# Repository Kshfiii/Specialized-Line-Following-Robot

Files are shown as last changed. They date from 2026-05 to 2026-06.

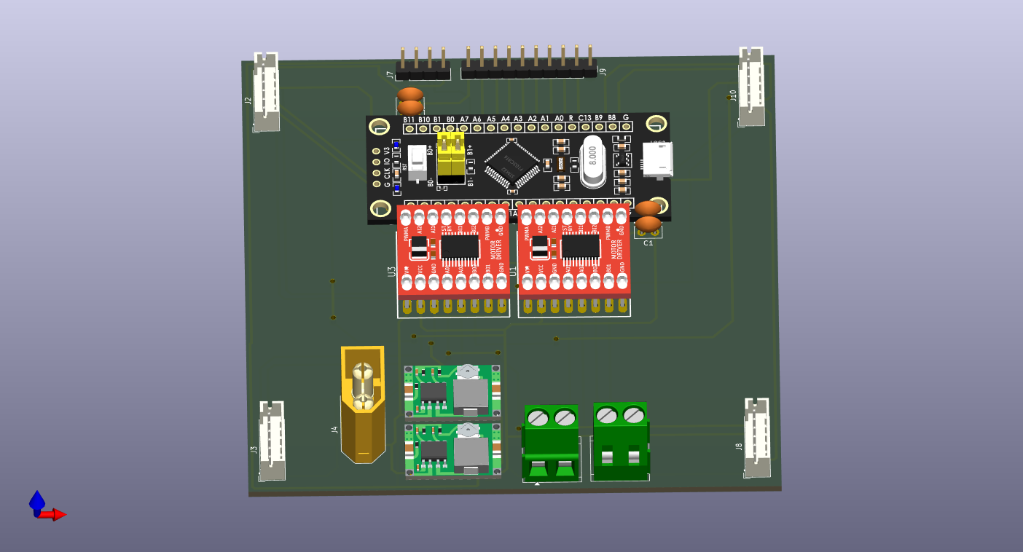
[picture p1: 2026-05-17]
PCB/LFR_Specialized.png

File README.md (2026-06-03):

# Specialized-Line-Following-Robot
Github (1000 x 350 px)

This is a specialized line follower robot with a custom built 8 Sensor Array, using tcrt5000 IR sensors, for sensing the lines. In addition to basic line following, the robot has a specialized function for dispensing pellets into designated spots, at different heights, for which it uses a scissor lift along with a conveyor belt system, powered by high torque n20 motors. It was made to compete in a robotics competition, NERC, and as a way to challenge myself to make a better LFR then the one I made before, which I think I have.

## About

<!-- This Project is powered by an 11.1v 3300 mah Li-po battery. It has 3 power rails; 11.1v, 5v, and <!- 3rd power line here ->, it uses two mini mp2307 to convert the voltages.-->
### 1. Robot function 
 
 
 

The robot follows a 3cm wide black line on the arena floor, maneuvering intersections & Zig Zag patterns on the arena floor. At Storage rack 1 (S1), a box of 7x7 inches supports the storage rack, with one of four faces colored blue. the robot must go around the box to detect the blue colored face, where the slot openings are present in the form of a 2x2 grid, as seen in the image above. The robot must detect strips below the slots as either blue or red, placing the pellets into the slots marked blue, and skipping over the red ones. The robot then heads to Storage rack 2 (S2), repeating the same procedure. Then, the robot travels through the zig zag pattern and climbs a ramp to reach Storage rack 3 (S3), After sucessful dispensing into designated slots at S3, it parks itself beyond the red line. 

### 2. Body
The body consists of three layers. The Base, the Middle, and the top most layer. 
 #### 2.1 The Base
Roboto (3)
The base is made of a custom 3d printed Chasis, housing four GA25-370 Motors and a battery on top with the IR Sensor Array Mounted to the bottom, Alongside extruded platforms for inserts.

##### 2.1.1 IR Sensor Array
Roboto (3)

<!-- add ss of 3d model from kicad & schematics-->
A custom built 8 channel analog IR sensor array bulit from tcrt5000 sensors. It uses 4.7k & 1k resistors. It also utilizes capacitors & an led that lights up when a sensor is returning a reading, serving as a checker to see if it works. 

#### 2.2 The Middle layer
Roboto (1)

<!-- add ss of middle layer from onshape, make a banner thing with lables in canva and put it here, layer has, acrylic base, spacers, pcb, hcsr04  -->
The Middle layer is supported by a laser cut acrylic sheet which is screwed on top of the 3d printed chasis using spacers. It consists of a custom built PCB & spacers along with the HC-SR04 ultrasonic sensor for distance measurement. 

##### 2.2.1 PCB
Roboto (5)
The pcb routes a 3300mah, 11.1v li-po battery pack through two mini MP2307 buck convertor, forming 3 power rails, 11.1v, 5v, and <!-- x volts --> which are used throughout the robot. The PCB houses the STM32F401 Microcontroller with two TB6612FNG motor driver breakout boards, one of which governs the motion of the GA25-370 motors and the other controls the N20 motors used for raising the scissor lift and moving the conveyor belt. It has headers for the IR sensors and the ultrasonic sensor.

#### 2.3 The Top layer
Roboto (8)
The top layer is also supported by a laser cut acrylic sheet which is screwed on top of the first acrylic sheet, separated by ~1.2in vertically, using spacers and nuts. It is home to the whole Pellet dispensing mechanism, The scissor lift, the Color sensing system and the conveyor belt.

##### 2.3.1 Scissor lift
<!-- add ss of 3d model from onshape, make a banner thing with lables in canva and put it here -->
The scissor lift is made entriely of a 3d printed body. It's movement is controlled by a high torque N20 gear motor which sits on the acrylic sheet. The collapsed height of the lift is <!-- x inches --> and it can streatch upto <!-- y inches --> 

##### 2.3.2 Color sensing system
<!-- add ss of 3d model from onshape, make a banner thing with lables in canva and put it here -->
The color sensing system consists of a Sg90 servo with a TCS34725 color sensor mounted to a 3d printed arm, which is screwed onto Sg90. The arm is <!-- z inches --> in length. The system is fixed underneath the top plate of the scissor lift, so that it can climb with the lift, giving it the ability to detect the color of the strips at both heights vertically. The servo rotates the arm 180° which allows the color sensor to detect both heights laterally. By using this system, the color sensor can cover the strips below each slot in the 2x2 grid.

##### 2.3.3 Conveyor belt
<!-- add ss of 3d model from onshape with the pellets stored and dimensions, make a banner thing with lables in canva and put it here -->
The conveyor belt is made of a 3d printed body. It uses a high torque N20 motor and bearings to rotate the pulleys, which drive the belt. The pellets sit on top of the belt, preloaded before the robot starts. 

## Assembly & Building
Go to [Onshape](https://cad.onshape.com/documents/1d0c454716dc1fb7909d87f9/w/77de741c5d18967e566ddcde/e/cc4241ede1b87dd95ef516c6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) Each part of the Line follower robot has been organized into folders. All print parts are consolidated in the 'To Print' tab on the bottom left. If confusion persists, you may contact me at: kasshafemman@gmail.com. Now follow along for each section.

### Body
Open the LFR Body Folder to see the CAD model. Now, using the brackets, fix the motors to the chasis. Put the wheels on the motor shaft. Put the insrts into the extruded square, then use it to screw Acrylic layer one. Put the PCB on this layer and the Ultrasonic sensor, within its bracket. Add a spacer and screw in Acrylic layer 2. Then put the scissor lift's extruded patterns (for the lack of a better word) on top of the complimentary slots on Acrylic layer 2.

### Scissor Lift:
Open Scissor lift folder for reference. Slide the scissor legs onto the shafts and put them in the place holders made on platform one. Use a string or pice of yarn, tying one end to the n20 motor and the other to the center of shaft 2. To prevent the shafts from sliding off, attach the knubs to the shaft's complementery ends. Now put pin 1 through one end of the hole in the scissor leg and pin 2 through the other, repeat this for all the arms to get the scissors pattern as shown in the assembly.

### Conveyor Belt
Open conveyor belt folder for reference. Put the supports into side plate 1 of the conveyor belt. Glue in bearings in the holes of both plates and put the pulleys inside the bearings. Now attach Side plate 2 on the other side. Put the conveyor belt onto the scissor lift, which had complementary holes to have it fixed in place.

## Robot Logic & Software
It is written in C++ using the Arduino framework on an STM32F401 (Black Pill). The code is split into six files, 'drive', 'sensors', 'Lift', 'nav' (short for navigation', 'pellet dispension' (color sensing + conveyor belt), with each of them handling one specific robot fuction, plus an additional 'config.h' where I put the tunable values.

Navigation is handled by the nav.cpp file, which uses a PID logic and values from the IR sensor array to stay on the line. The Wheel encodersb give additional feedback, measuring the distance traveled, and the HC-SR04 ultrasonic sensor confirms when the robot is close enough to a rack for dispensing.

At each station, the robot scans the rack using the color sensing mechanism. The TCS34725 is aligned so that it faces the colored strip. It takes several readings at its position, so that it can detect the color of the strip reliably. If the strip is blue, the robot alligns itself with the rack and a pellet is dispensed. After that, the servo rotates 180°, sensing the other strip laterally. The process is repeated for both the lower and upper rows of the rack, the lift raises the sensor and dispenser to reach the upper row. Additionally, Color readings are normalized to reduce the effect of changing lighting conditions.

The robot follows the black line, navigating to S1, dropping the pellets, Then repeating the same for S2, then climbs the ramp to S3, drops the pellets and parks itself beyond the finsih line. `nav.cpp` handles line following using a PID controller on the IR array's weighted error, with encoder ticks tracking distance from the last known point and the HC-SR04 confirming when the rack face is actually in range.

The servicing routine is the same for all three units. The robot closes in on the rack, sweeps the color sensor servo left and right at the lower row, reads the TCS34725 five times per position, nudges left or right and ejects into whichever slots came back blue, then raises the lift and repeats for the upper row. Color detection normalizes against the clear channel so arena lighting doesn't throw it off.

### Dependencies
To work, the firmware needs:
- STM32duino core
- `Adafruit_TCS34725` via Arduino Library Manager
- `Wire` and `Servo` ship with the core

## Component List
1. STM32F401 (Blackpill) Microcontroller
2. B6612FNG Motor Driver
3. JGA25-370 Motor with wheels and Brackets
4. TCRT5000 IR sensors
5. Resistors and capacitors
6. 11.1v 3300mAh Lipo Battery
7. High torque N20 Motors
8. TCS34725 Color Sensor
9. Hc-sr04 Ultrasonic Sensor
10. Bearings
11. Acrylic sheet

## Bill of Materials
| Component | Quantity | Est. Cost (USD) | Purchase Links | 
| :--- | :---: | :--- | :--- |
| **PLA Filament**| 1 | $16.55 |[Link](https://electrobes.com/product/exyz-pla-1-75mm-3d-printer-filament-1kg-roll/)| 
| **11.1v 3300mAh Lipo Battery** | 1 | $24.00 | [Link](https://colgroad.com/product/zop-power-3s-11-1v-3300mah-25c-lipo-battery/) | 
| **JGA25-370 Motor kit** | 4 | $48.00 | [Link](https://colgroad.com/product/dc-gear-motor-with-encoder-280rpm-620rpm-ga25-370-complete-kit/)| 
| **TCRT5000 IR sensors** | 10 | $03.40 |[Link](https://epro.pk/product/tcrt5000-reflective-optical-ir-sensor-in-pakistan/)| 
| **Resistors** | 2 | $00.50 |[Link](https://epro.pk/product/1206-smd-resistor-smd-1206-tolerance-5-smd-resistor-1206-pack-of-10-pcs-2/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)| 
| **SMD LED** | 2 | $00.75 |[Link](https://digilog.pk/products/100pcs-smd-0805-led-smt-led-light-diode?variant=49762233876758)| 
| **Hc-sr04 Ultrasonic Sensor** | 1 | $00.72 | [Link](https://epro.pk/product/ultrasonic-sensor-hc-sr04-in-pakistan/) | 
| **Standoff** | 2 | $00.25 |[Link](https://epro.pk/product/brass-standoff-spacer-screw-long-pillars-nut/)| 
| **Mp2307 Buck convertor** | 2 | $00.90 |[Link](https://epro.pk/product/dc-to-dc-step-down-mini-360-buck-converter-module/)| 
| **6 pin Jst-xh connector** | 4 | $00.14 |[Link](https://digilog.pk/products/6-pin-2-5mm-jst-xh-style-male-connector-in-pakistan)| 
| **Xt60 Lipo battery connector** | 1 | $00.65 |[Link](https://epro.pk/product/xt60connectorsmalefemalepairinpakistan/)| 
| **Sg90 Servo Motor** | 1 | $1.15 |[Link](https://epro.pk/product/tower-pro-sg90-9g-micro-servo-motor-with-accessories-blue/)| 
| **STM32F401**| 1 | $03.55 |[Link](https://epro.pk/product/stm32f401-development-board/)| 
| **TB6612FNG Motor Driver**| 1 | $02.00 | [Link](https://epro.pk/product/tb6612-drv8833-dual-motor-driver-module-1a-h-bridge-for-arduino-robotics/) | 
| **200 RPM N20 Motors** | 2 | $03.00 | [Link](https://colgroad.com/product/n20-mini-dc-gear-motor-200-600-800-1000-rpm-brand-new/) | 
| **TCS34725 Color Sensor** | 1 | $03.58 | [Link](https://digilog.pk/products/tcs34725-color-sensor-module-pakistan) | 
| **Bearings** | 1 | $4.30 | [Link](https://epro.pk/product/cnc-v-slot-bearing-open-builds-wheel-pom-mr105zz-625zz-bore-5mm-passive-round-gear/) | 
| **Acrylic sheet** | 2 | $03.23 | [Link](https://www.daraz.pk/products/acrylic-sheet-2mm-size-12x12-2mm-thick-i391245284.html)| 
| **Total Build Cost:** |  | **~$120.00** |

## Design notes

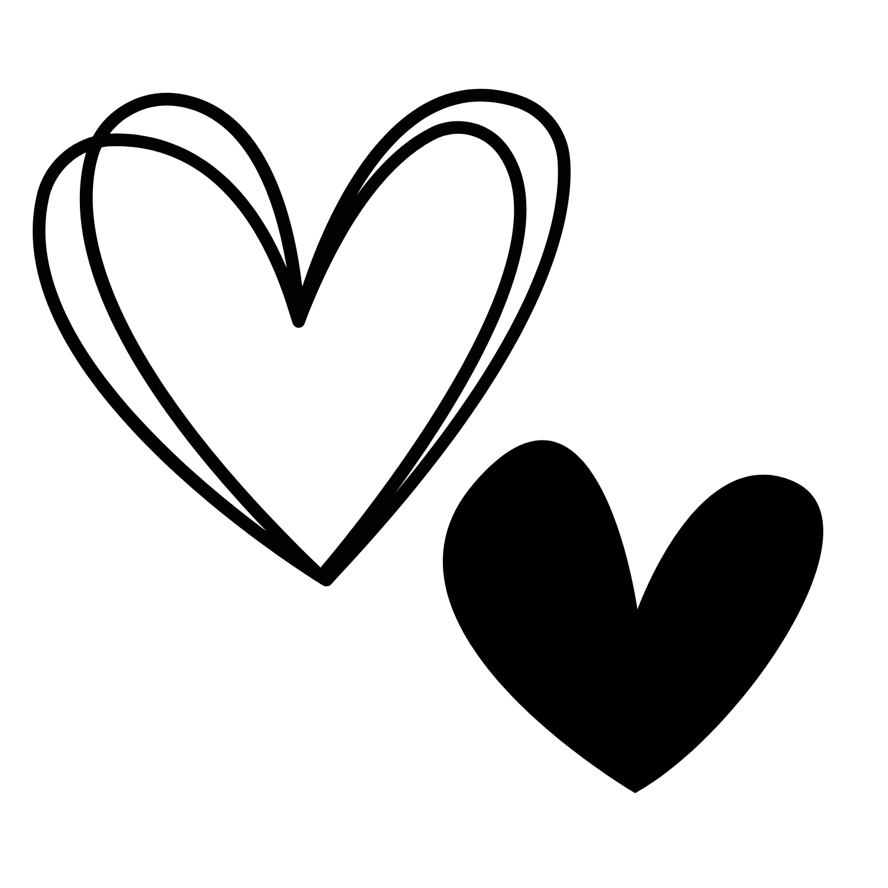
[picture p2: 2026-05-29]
IR_Array/Untitled design (2).png

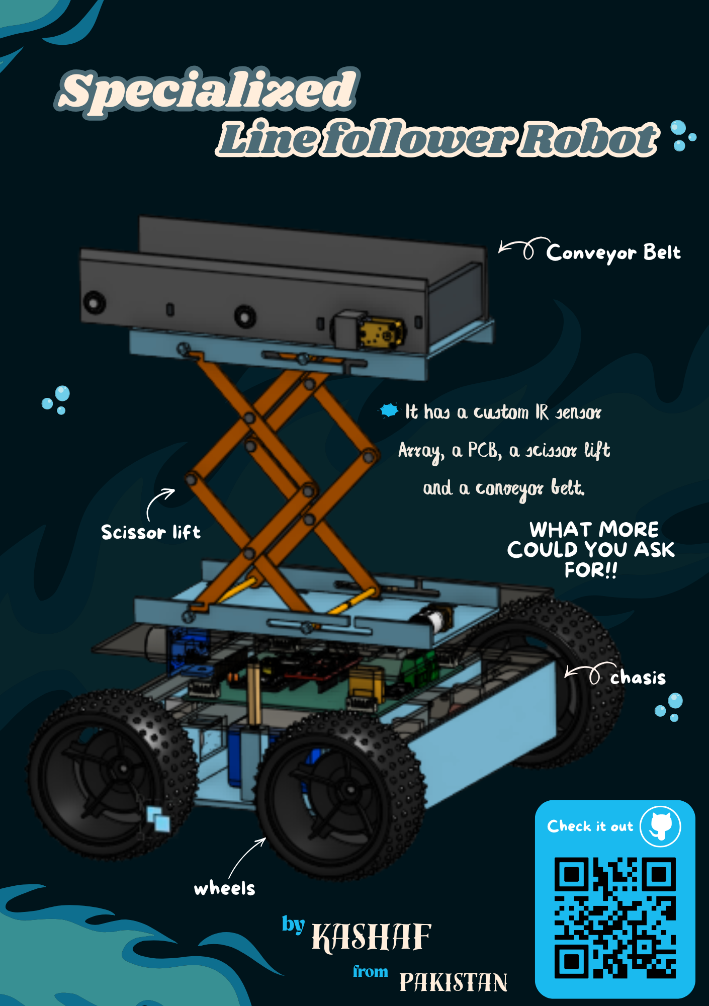
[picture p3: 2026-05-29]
LFR_Zine.png

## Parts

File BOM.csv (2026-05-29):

Component | Quantity | Est. Cost (USD) | Purchase Links
STM32F401 | 1 | $03.55 | https://epro.pk/product/stm32f401-development-board/
TB6612FNG Motor Driver | 1 | $02.00 | https://epro.pk/product/tb6612-drv8833-dual-motor-driver-module-1a-h-bridge-for-arduino-robotics/
JGA25-370 Motor kit | 4 | $24.00 | https://colgroad.com/product/dc-gear-motor-with-encoder-280rpm-620rpm-ga25-370/
QTR 8C IR Sensor Array | 2 | $04.59 | https://epro.pk/product/qtr-8rc-line-following-reflectance-ir-sensor-8-channel-line-following-line-tracking-array-module/
11.1v 3300mAh Lipo Battery | 1 | $24.00 | https://colgroad.com/product/zop-power-3s-11-1v-3300mah-25c-lipo-battery/
200 RPM N20 Motors | 2 | $03.00 | https://colgroad.com/product/n20-mini-dc-gear-motor-200-600-800-1000-rpm-brand-new/
TCS34725 Color Sensor | 1 | $03.58 | https://digilog.pk/products/tcs34725-color-sensor-module-pakistan
Hc-sr04 Ultrasonic Sensor | 1 | $00.72 | https://epro.pk/product/ultrasonic-sensor-hc-sr04-in-pakistan/
Bearings | 1 | $4.30 | https://epro.pk/product/cnc-v-slot-bearing-open-builds-wheel-pom-mr105zz-625zz-bore-5mm-passive-round-gear
Acrylic sheet | 2 | $03.23 | https://www.daraz.pk/products/acrylic-sheet-2mm-size-12x12-2mm-thick-i391245284.html
Total Build Cost: |  | ~$70.00

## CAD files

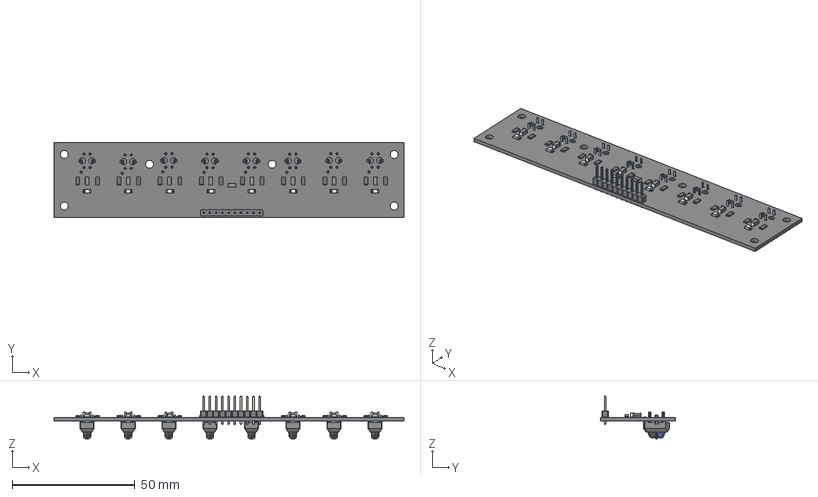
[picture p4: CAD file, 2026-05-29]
IR_Array/IR_Array.step
142.8 x 30.4 x 17.4 mm
C_1206_3216Metric x 9
R_1206_3216Metric x 16
LED_1206_3216Metric x 8
PinHeader_1x10_P2.54mm_Vertical
TCRT5000--3DModel-STEP-56544 x 8
IR_Array_PCB

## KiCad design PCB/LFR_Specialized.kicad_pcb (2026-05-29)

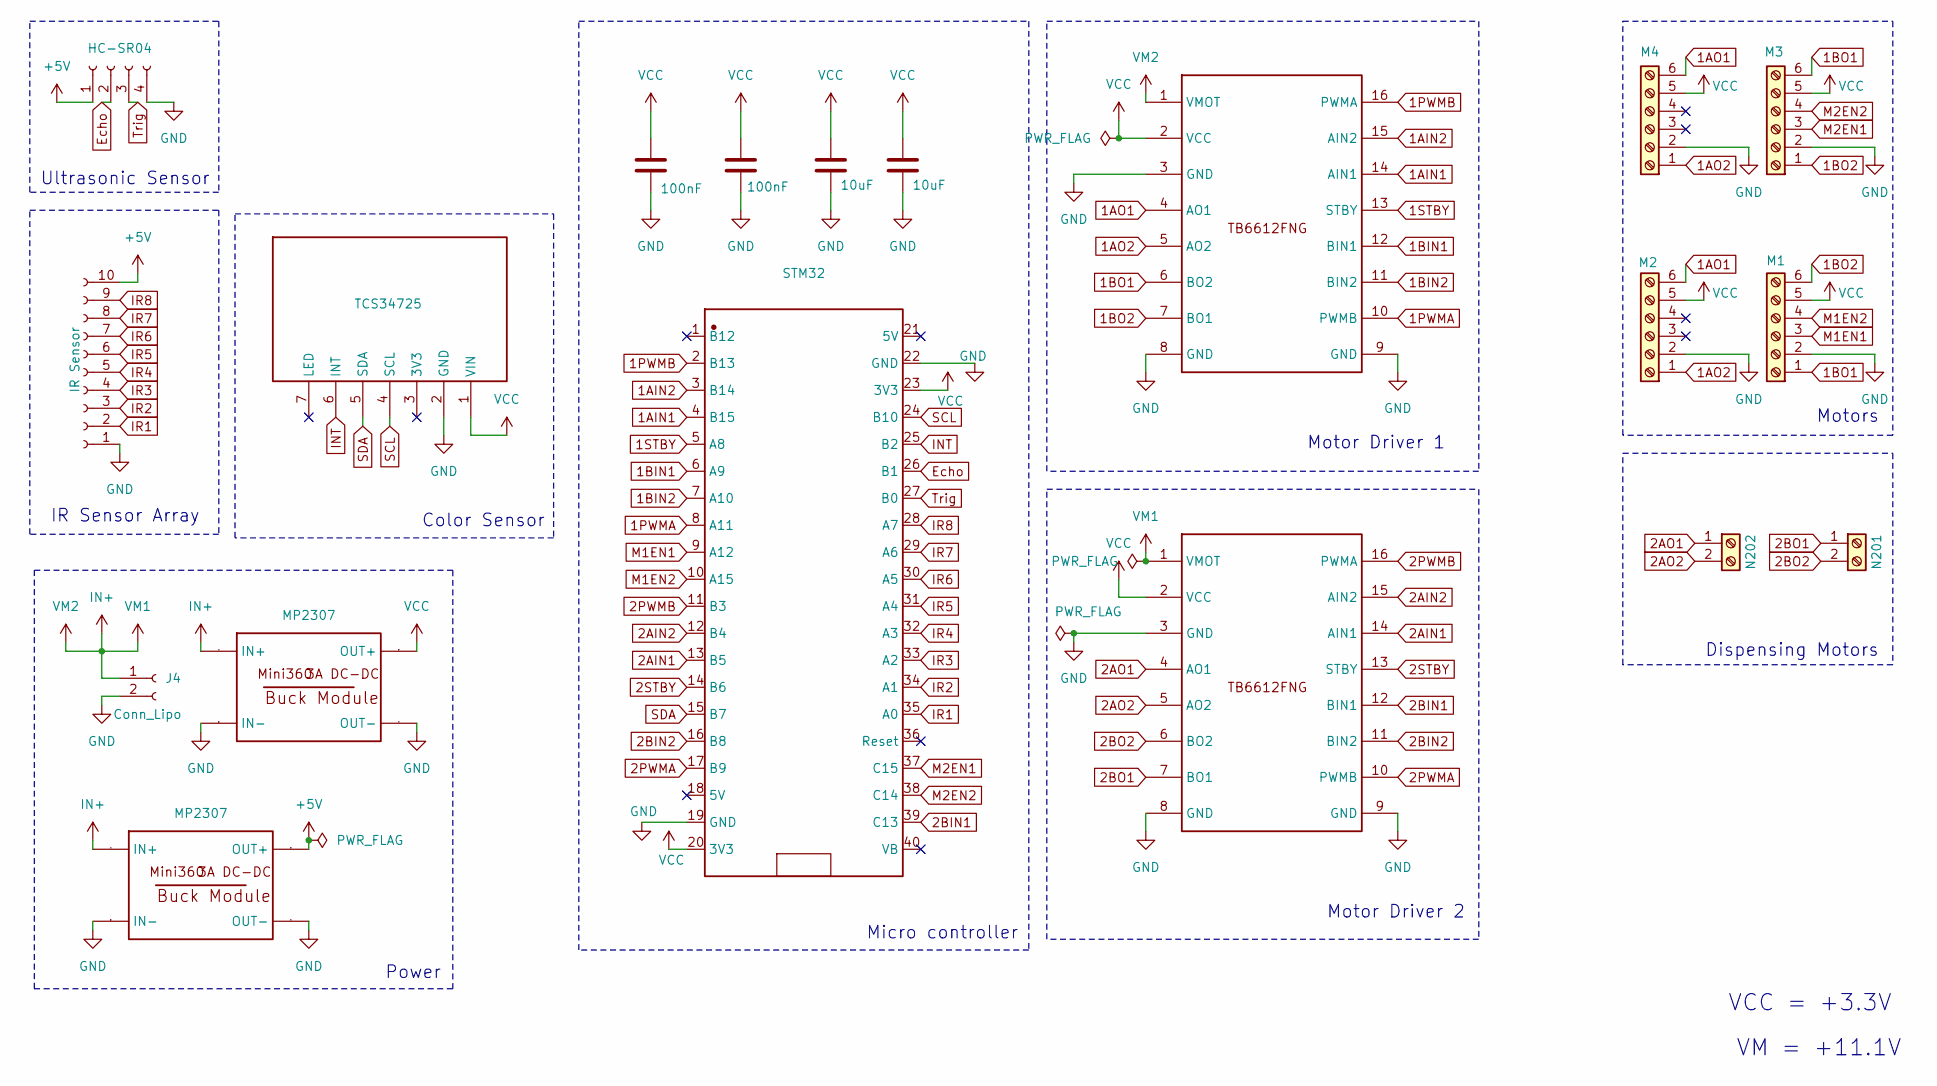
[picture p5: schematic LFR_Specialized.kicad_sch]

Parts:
C1, C12: 10uF; C_Disc_D5.0mm_W2.5mm_P2.50mm
C9, C11: 100nF; C_Disc_D5.0mm_W2.5mm_P2.50mm
J2: M1; JST_PH_B6B-PH-K_1x06_P2.00mm_Vertical
J3: M2; JST_PH_B6B-PH-K_1x06_P2.00mm_Vertical
J4: Conn_Lipo; AMASS_XT60-M_1x02_P7.20mm_Vertical
J5: N201; terminal
J6: N202; terminal
J7: HC-SR04; PinHeader_1x04_P2.54mm_Vertical
J8: M4; JST_PH_B6B-PH-K_1x06_P2.00mm_Vertical
J9: IR Sensor; PinHeader_1x10_P2.54mm_Vertical
J10: M3; JST_PH_B6B-PH-K_1x06_P2.00mm_Vertical
P1: TCS34725; PinHeader_1x07_P2.54mm_Vertical
STM32: STM32F401CC-WEACTBOARD-FOOTPRINT
U1, U3: TB6612FNG Dual Motor Driver SparkFun; TB6612FNG-BREAKOUT
U2, U4: MP2307; MINI360 BUCK CONVERTOR

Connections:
1AIN1: STM32.4 (B15), U3.14 (AIN1)
1AIN2: STM32.3 (B14), U3.15 (AIN2)
1AO1: J3.6, J8.6, U3.4 (AO1)
1AO2: J3.1, J8.1, U3.5 (AO2)
1BIN1: STM32.6 (A9), U3.12 (BIN1)
1BIN2: STM32.7 (A10), U3.11 (BIN2)
1BO1: J2.1, J10.6, U3.6 (BO2)
1BO2: J2.6, J10.1, U3.7 (BO1)
1PWMA: STM32.8 (A11), U3.10 (PWMB)
1PWMB: STM32.2 (B13), U3.16 (PWMA)
1STBY: STM32.5 (A8), U3.13 (STBY)
2AIN1: STM32.13 (B5), U1.14 (AIN1)
2AIN2: STM32.12 (B4), U1.15 (AIN2)
2AO1: J6.1, U1.4 (AO1)
2AO2: J6.2, U1.5 (AO2)
2BIN1: STM32.39 (C13), U1.12 (BIN1)
2BIN2: STM32.16 (B8), U1.11 (BIN2)
2BO1: J5.1, U1.7 (BO1)
2BO2: J5.2, U1.6 (BO2)
2PWMA: STM32.17 (B9), U1.10 (PWMB)
2PWMB: STM32.11 (B3), U1.16 (PWMA)
2STBY: STM32.14 (B6), U1.13 (STBY)
Echo: J7.2, STM32.26 (B1)
GND: C1.2, C9.2, C11.2, C12.2, J2.2, J3.2, J4.2, J7.4, J8.2, J9.1, J10.2, P1.2 (GND), STM32.19 (GND), STM32.22 (GND), U1.3 (GND), U1.8 (GND), U1.9 (GND), U2.1 (IN-), U2.3 (OUT-), U3.3 (GND), U3.8 (GND), U3.9 (GND), U4.1 (IN-), U4.3 (OUT-)
IN+: J4.1, U1.1 (VMOT), U2.2 (IN+), U3.1 (VMOT), U4.2 (IN+)
INT: P1.6 (INT), STM32.25 (B2)
IR1: J9.2, STM32.35 (A0)
IR2: J9.3, STM32.34 (A1)
IR3: J9.4, STM32.33 (A2)
IR4: J9.5, STM32.32 (A3)
IR5: J9.6, STM32.31 (A4)
IR6: J9.7, STM32.30 (A5)
IR7: J9.8, STM32.29 (A6)
IR8: J9.9, STM32.28 (A7)
M1EN1: J2.3, STM32.9 (A12)
M1EN2: J2.4, STM32.10 (A15)
M2EN1: J10.3, STM32.37 (C15)
M2EN2: J10.4, STM32.38 (C14)
SCL: P1.4 (SCL), STM32.24 (B10)
SDA: P1.5 (SDA), STM32.15 (B7)
Trig: J7.3, STM32.27 (B0)

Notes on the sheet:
VM = +11.1V
Ultrasonic Sensor
Power
Dispensing Motors
Motors
Micro controller
Motor Driver 2
Color Sensor
IR Sensor Array
Motor Driver 1
VCC = +3.3V

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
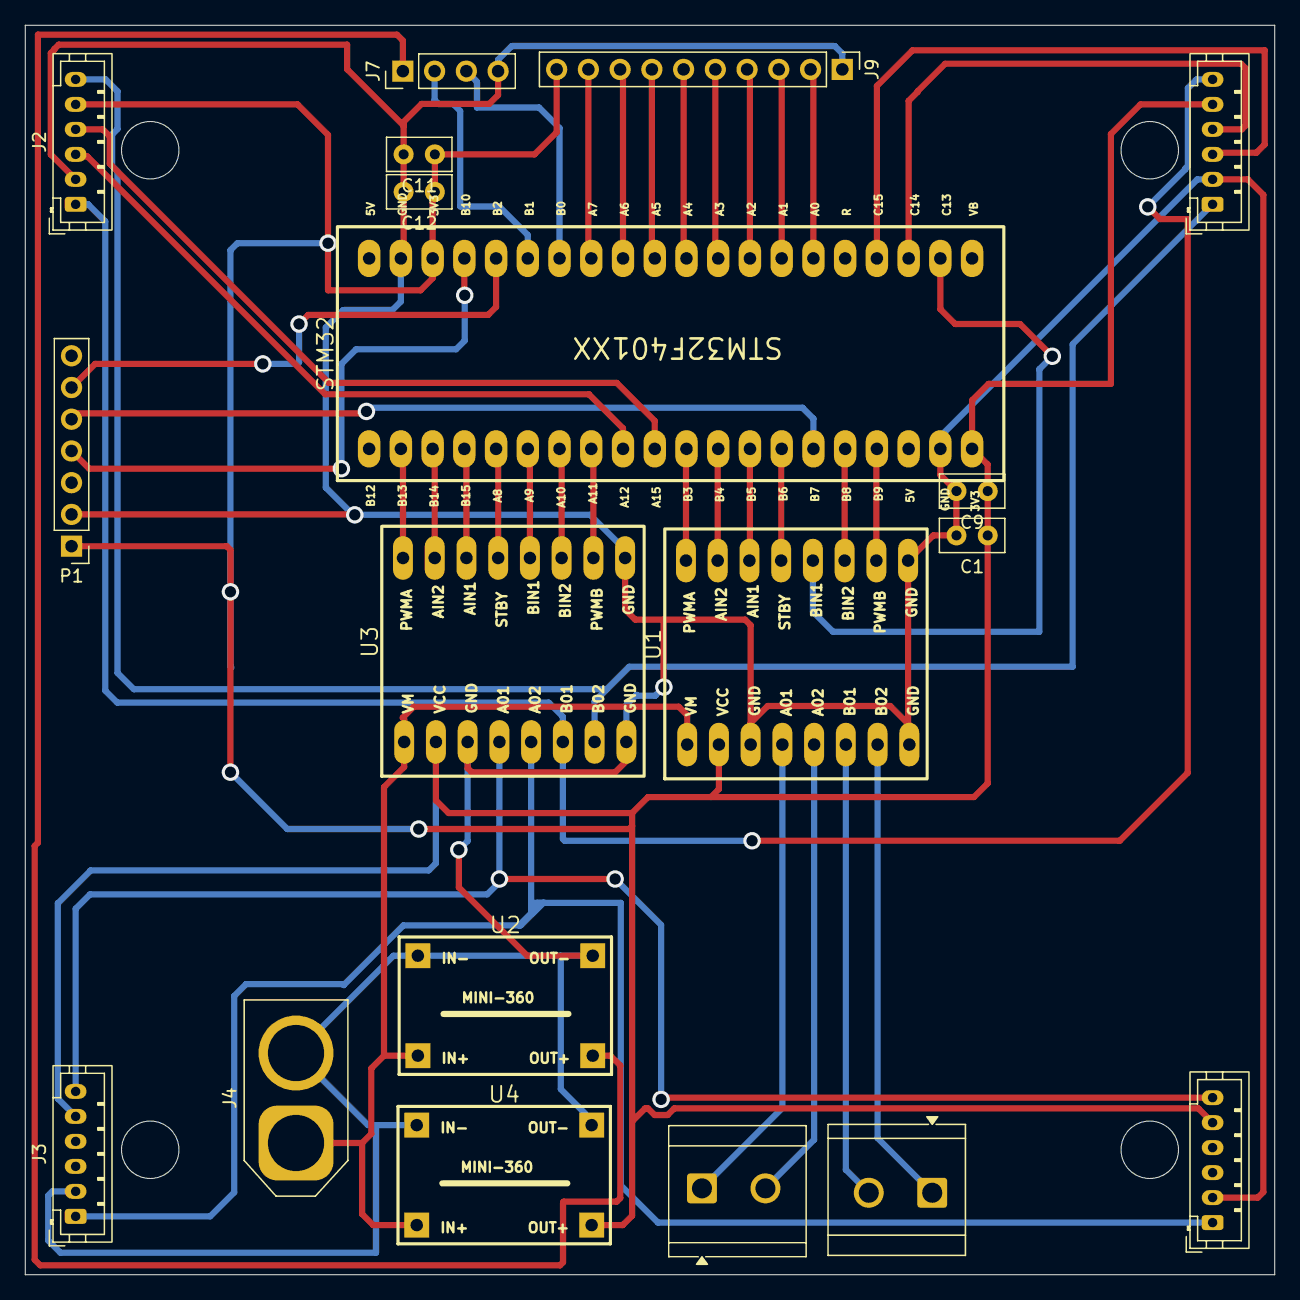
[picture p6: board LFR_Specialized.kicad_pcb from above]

Board: 2 copper layers, 100.0 x 100.0 mm, 19 parts (0 on the bottom side), 43 nets.

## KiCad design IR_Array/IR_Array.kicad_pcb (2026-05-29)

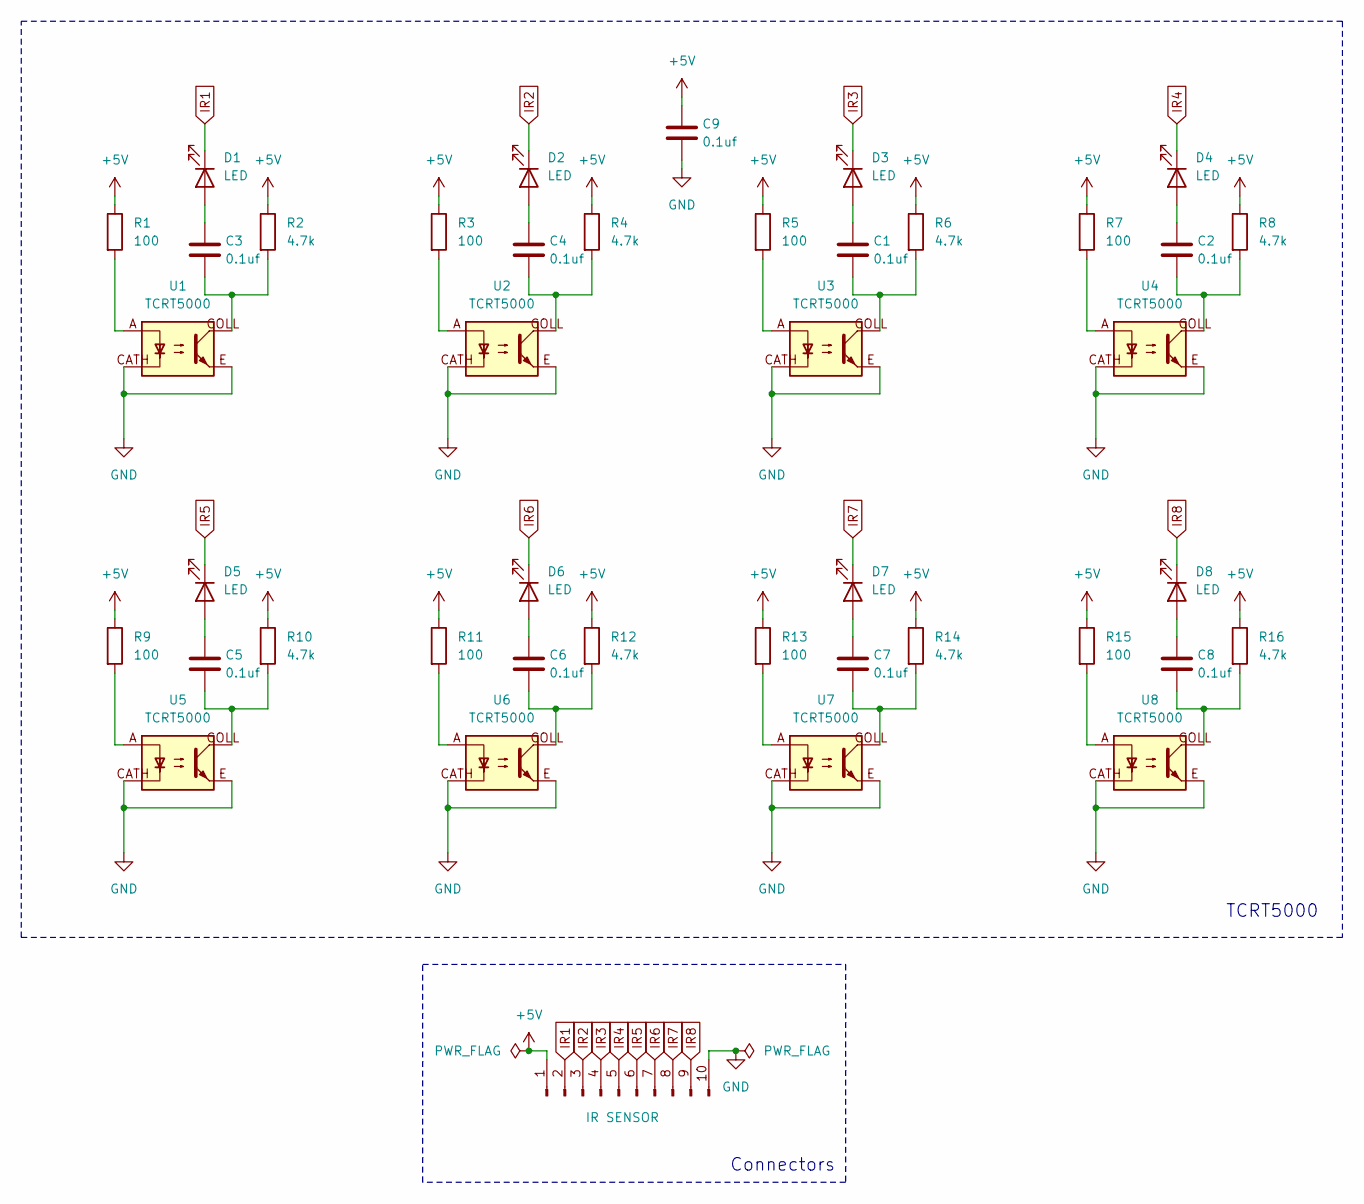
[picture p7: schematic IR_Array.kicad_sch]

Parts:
C1, C2, C3, C4, C5, C6, C7, C8, C9: 0.1uf; C_1206_3216Metric_Pad1.33x1.80mm_HandSolder
D1, D2, D3, D4, D5, D6, D7, D8: LED; LED_1206_3216Metric_Pad1.42x1.75mm_HandSolder
J1: IR SENSOR; PinHeader_1x10_P2.54mm_Vertical
R1, R3, R5, R7, R9, R11, R13, R15: 100; R_1206_3216Metric_Pad1.30x1.75mm_HandSolder
R2, R4, R6, R8, R10, R12, R14, R16: 4.7k; R_1206_3216Metric_Pad1.30x1.75mm_HandSolder
U1, U2, U3, U4, U5, U6, U7, U8: TCRT5000; tcrt5000

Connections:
+5V: C9.1, J1.1, R1.1, R2.1, R3.1, R4.1, R5.1, R6.1, R7.1, R8.1, R9.1, R10.1, R11.1, R12.1, R13.1, R14.1, R15.1, R16.1
GND: C9.2, J1.10, U1.CATH, U1.E, U2.CATH, U2.E, U3.CATH, U3.E, U4.CATH, U4.E, U5.CATH, U5.E, U6.CATH, U6.E, U7.CATH, U7.E, U8.CATH, U8.E
IR1: D1.1 (K), J1.2
IR2: D2.1 (K), J1.3
IR3: D3.1 (K), J1.4
IR4: D4.1 (K), J1.5
IR5: D5.1 (K), J1.6
IR6: D6.1 (K), J1.7
IR7: D7.1 (K), J1.8
IR8: D8.1 (K), J1.9
unnamed: C1.2, R6.2, U3.COLL
unnamed: C2.2, R8.2, U4.COLL
unnamed: C3.2, R2.2, U1.COLL
unnamed: C4.2, R4.2, U2.COLL
unnamed: C5.2, R10.2, U5.COLL
unnamed: C6.2, R12.2, U6.COLL
unnamed: C7.2, R14.2, U7.COLL
unnamed: C8.2, R16.2, U8.COLL
unnamed: C3.1, D1.2 (A)
unnamed: C4.1, D2.2 (A)
unnamed: C1.1, D3.2 (A)
unnamed: C2.1, D4.2 (A)
unnamed: C5.1, D5.2 (A)
unnamed: C6.1, D6.2 (A)
unnamed: C7.1, D7.2 (A)
unnamed: C8.1, D8.2 (A)
unnamed: R1.2, U1.A
unnamed: R3.2, U2.A
unnamed: R5.2, U3.A
unnamed: R7.2, U4.A
unnamed: R9.2, U5.A
unnamed: R11.2, U6.A
unnamed: R13.2, U7.A
unnamed: R15.2, U8.A

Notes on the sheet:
Connectors
TCRT5000

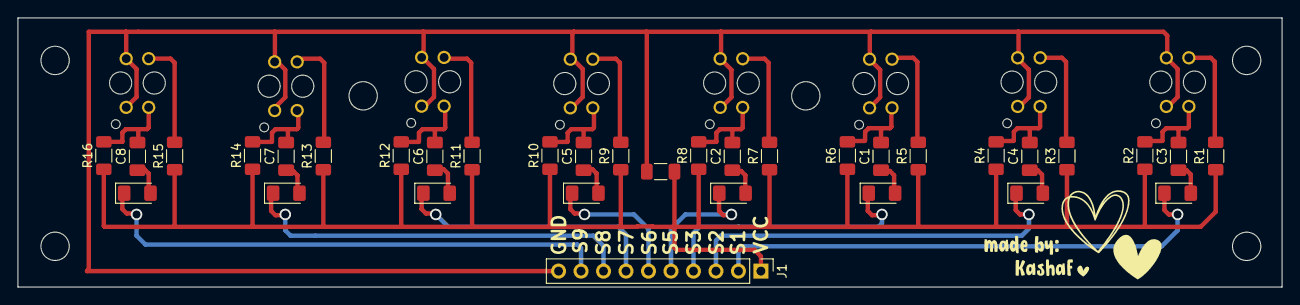
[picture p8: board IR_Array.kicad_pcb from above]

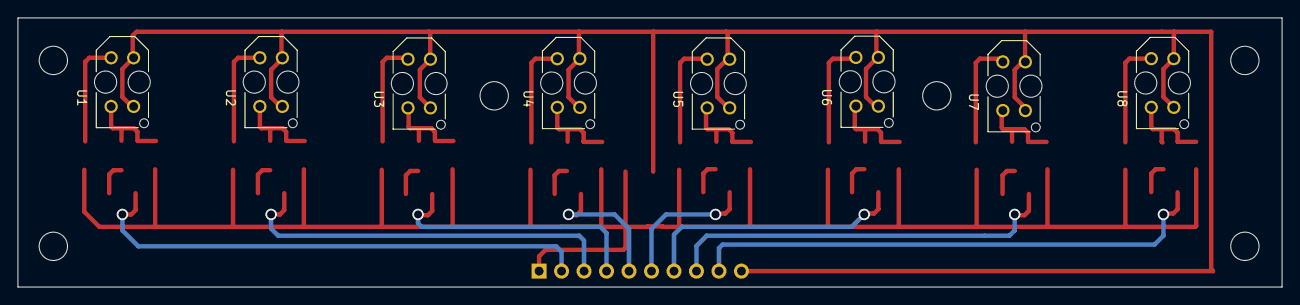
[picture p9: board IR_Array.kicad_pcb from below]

Board: 2 copper layers, 142.8 x 30.4 mm, 42 parts (8 on the bottom side), 34 nets.

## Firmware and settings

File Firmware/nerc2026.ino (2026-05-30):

#include <Arduino.h>
#include "config.h"
#include "drive.h"
#include "sensors.h"
#include "lift.h"
#include "nav.h"
#include "sm.h"

void setup() {
    Serial.begin(115200);

    pinMode(START_BTN, INPUT_PULLUP);
    pinMode(STATUS_LED, OUTPUT);
    digitalWrite(STATUS_LED, HIGH);

    driveInit();
    liftInit();
    sensorsInit();
    colorInit();
    navInit();
    smInit();

    while (digitalRead(START_BTN) == HIGH) delay(10);
    delay(150);

    digitalWrite(STATUS_LED, LOW);
    smStart();
}

void loop() {
    smTick();
    delay(5);
}

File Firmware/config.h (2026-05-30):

#pragma once
#include <Arduino.h>

// ── drive TB6612FNG ─────────────────────────────────────────────────────────
// left motors (FL + BL wired in parallel on channel A)
#define DRV_STBY    PA6
#define L_IN1       PA0
#define L_IN2       PA1
#define L_PWM       PA2
// right motors (FR + BR wired in parallel on channel B)
#define R_IN1       PA3
#define R_IN2       PA4
#define R_PWM       PA5

// ── mechanism TB6612FNG ─────────────────────────────────────────────────────
#define MCH_STBY    PA7
#define LFT_IN1     PB0
#define LFT_IN2     PB1
#define LFT_PWM     PB3
#define CNV_IN1     PB4
#define CNV_IN2     PB5
#define CNV_PWM     PB8

// ── servo, encoders, sonar ──────────────────────────────────────────────────
#define SERVO_PIN   PB9
#define ENC_L       PB10
#define ENC_R       PB11
#define SONAR_TRIG  PB12
#define SONAR_ECHO  PB13

// ── IR array (6 sensors, left → right) ─────────────────────────────────────
#define IR_COUNT 6
const uint8_t IR_PINS[IR_COUNT] = { PA8, PA11, PA12, PB14, PB15, PA15 };
// IR_PINS[i] == HIGH  →  sensor over black line (adjust polarity if inverted)

// ── TCS34725 on Wire (I2C1: PB6=SCL  PB7=SDA) ──────────────────────────────

// ── misc ────────────────────────────────────────────────────────────────────
#define START_BTN   PB2
#define STATUS_LED  PC13   // active LOW on Black Pill

// ── drive tuning ────────────────────────────────────────────────────────────
#define DRIVE_BASE   155
#define DRIVE_MAX    220
#define TURN_SPEED   130
#define RAMP_SPEED   DRIVE_MAX

// ── PID ─────────────────────────────────────────────────────────────────────
#define KP  0.40f
#define KI  0.00f
#define KD  0.20f

// ── encoder odometry ────────────────────────────────────────────────────────
#define TICKS_PER_CM   21      // calibrate on actual surface

// ── sonar thresholds (cm) ───────────────────────────────────────────────────
#define SONAR_RACK_CM   8
#define SONAR_WALL_CM   12

// ── distances from start to each target (cm) ────────────────────────────────
#define DIST_TO_S1      60
#define DIST_S1_TO_S2   105
#define DIST_S2_TO_RAMP 140

// ── lift timing ─────────────────────────────────────────────────────────────
#define LIFT_SPEED      180
#define LIFT_RAISE_MS   1100   // time to reach upper row from collapsed
#define LIFT_LOWER_MS   1100

// ── conveyor ────────────────────────────────────────────────────────────────
#define CONV_SPEED      210
#define CONV_EJECT_MS   750

// ── servo sweep angles ───────────────────────────────────────────────────────
#define SERVO_LEFT   35
#define SERVO_RIGHT  145
#define SERVO_MID    90

// ── slot lateral alignment ───────────────────────────────────────────────────
// brief timed nudge to align conveyor exit with left or right slot
#define NUDGE_SPEED    100
#define NUDGE_MS       160     // tune until conveyor lines up with slot center
#define NUDGE_SETTLE   80

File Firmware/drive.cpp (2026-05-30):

#include "drive.h"
#include "config.h"

static void setMotor(uint8_t in1, uint8_t in2, uint8_t pwm, int spd) {
    if (spd > 0) {
        digitalWrite(in1, HIGH);
        digitalWrite(in2, LOW);
    } else if (spd < 0) {
        digitalWrite(in1, LOW);
        digitalWrite(in2, HIGH);
        spd = -spd;
    } else {
        digitalWrite(in1, LOW);
        digitalWrite(in2, LOW);
    }
    analogWrite(pwm, constrain(spd, 0, 255));
}

void driveInit() {
    pinMode(DRV_STBY, OUTPUT);
    pinMode(L_IN1, OUTPUT); pinMode(L_IN2, OUTPUT); pinMode(L_PWM, OUTPUT);
    pinMode(R_IN1, OUTPUT); pinMode(R_IN2, OUTPUT); pinMode(R_PWM, OUTPUT);
    digitalWrite(DRV_STBY, HIGH);
    driveStop();
}

void driveSetLeft(int spd)  { setMotor(L_IN1, L_IN2, L_PWM, spd); }
void driveSetRight(int spd) { setMotor(R_IN1, R_IN2, R_PWM, spd); }

void driveStop() {
    driveSetLeft(0);
    driveSetRight(0);
}

void driveFwd(int spd) {
    driveSetLeft(spd);
    driveSetRight(spd);
}

void driveRev(int spd) {
    driveSetLeft(-spd);
    driveSetRight(-spd);
}

void driveTurnLeft(int spd) {
    driveSetLeft(-spd);
    driveSetRight(spd);
}

void driveTurnRight(int spd) {
    driveSetLeft(spd);
    driveSetRight(-spd);
}

void driveNudgeLeft() {
    driveSetLeft(-NUDGE_SPEED);
    driveSetRight(NUDGE_SPEED);
    delay(NUDGE_MS);
    driveStop();
    delay(NUDGE_SETTLE);
}

void driveNudgeRight() {
    driveSetLeft(NUDGE_SPEED);
    driveSetRight(-NUDGE_SPEED);
    delay(NUDGE_MS);
    driveStop();
    delay(NUDGE_SETTLE);
}

void driveNudgeBack() {
    driveRev(NUDGE_SPEED);
    delay(NUDGE_MS);
    driveStop();
    delay(NUDGE_SETTLE);
}

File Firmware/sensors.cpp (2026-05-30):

#include "sensors.h"
#include "config.h"
#include <Wire.h>
#include <Adafruit_TCS34725.h>

static Adafruit_TCS34725 tcs = Adafruit_TCS34725(
    TCS34725_INTEGRATIONTIME_50MS,
    TCS34725_GAIN_4X
);

volatile long encL = 0;
volatile long encR = 0;

static void isrEncL() { encL++; }
static void isrEncR() { encR++; }

void sensorsInit() {
    for (int i = 0; i < IR_COUNT; i++) {
        pinMode(IR_PINS[i], INPUT);
    }
    pinMode(SONAR_TRIG, OUTPUT);
    pinMode(SONAR_ECHO, INPUT);
    digitalWrite(SONAR_TRIG, LOW);

    pinMode(ENC_L, INPUT_PULLUP);
    pinMode(ENC_R, INPUT_PULLUP);
    attachInterrupt(digitalPinToInterrupt(ENC_L), isrEncL, RISING);
    attachInterrupt(digitalPinToInterrupt(ENC_R), isrEncR, RISING);
}

void colorInit() {
    Wire.begin();
    if (!tcs.begin()) {
        pinMode(STATUS_LED, OUTPUT);
        while (1) {
            digitalWrite(STATUS_LED, !digitalRead(STATUS_LED));
            delay(150);
        }
    }
}

void irRead(bool *out) {
    for (int i = 0; i < IR_COUNT; i++) {
        out[i] = (digitalRead(IR_PINS[i]) == HIGH);
    }
}

int irError() {
    bool s[IR_COUNT];
    irRead(s);
    static const int W[IR_COUNT] = { -5, -3, -1, 1, 3, 5 };
    int sum = 0, cnt = 0;
    for (int i = 0; i < IR_COUNT; i++) {
        if (s[i]) { sum += W[i]; cnt++; }
    }
    return cnt ? sum / cnt : 0;
}

bool irJunction() {
    bool s[IR_COUNT];
    irRead(s);
    int cnt = 0;
    for (int i = 0; i < IR_COUNT; i++) if (s[i]) cnt++;
    return cnt >= 4;
}

bool irAllBlack() {
    bool s[IR_COUNT];
    irRead(s);
    for (int i = 0; i < IR_COUNT; i++) if (!s[i]) return false;
    return true;
}

float sonarCm() {
    digitalWrite(SONAR_TRIG, HIGH);
    delayMicroseconds(10);
    digitalWrite(SONAR_TRIG, LOW);
    long dur = pulseIn(SONAR_ECHO, HIGH, 25000UL);
    return dur ? dur / 58.0f : 999.0f;
}

void encoderReset() {
    noInterrupts();
    encL = 0;
    encR = 0;
    interrupts();
}

long encoderAvg() {
    noInterrupts();
    long l = encL, r = encR;
    interrupts();
    return (l + r) / 2;
}

SlotColor colorRead() {
    int blue = 0, red = 0;
    for (int i = 0; i < 5; i++) {
        uint16_t r, g, b, c;
        tcs.getRawData(&r, &g, &b, &c);
        if (c == 0) { delay(60); continue; }
        float rn = (float)r / c;
        float bn = (float)b / c;
        if      (bn > rn * 1.4f) blue++;
        else if (rn > bn * 1.4f) red++;
        delay(60);
    }
    if (blue >= 3) return COLOR_BLUE;
    if (red  >= 3) return COLOR_RED;
    return COLOR_UNKNOWN;
}

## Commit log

2026-05-06 Update price for QTR 8C IR Sensor Array
    Updated the price of the QTR 8C IR Sensor Array from $05.00 to $04.59.
2026-05-17 Update Bill of Materials with new components and costs
2026-05-28 Enhance README with detailed body structure and BOM
    Expanded the body section with detailed descriptions of the robot's layers, including the base, middle, and top layers, along with their components and functionalities. Added a bill of materials for 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
2026-05-29 Add Bill of Materials with components and costs
    [BOM.csv]
2026-05-29 Update BOM.csv with new formatting and links
    [BOM.csv]
